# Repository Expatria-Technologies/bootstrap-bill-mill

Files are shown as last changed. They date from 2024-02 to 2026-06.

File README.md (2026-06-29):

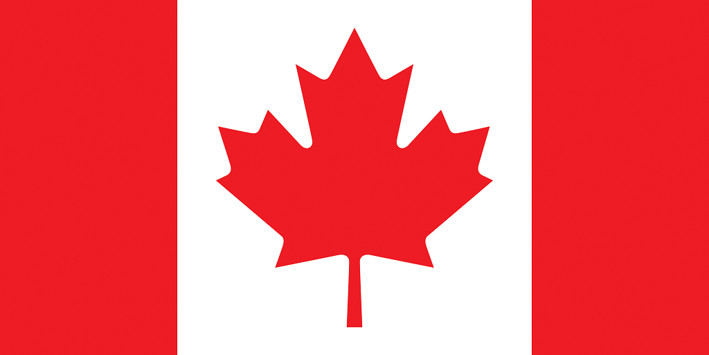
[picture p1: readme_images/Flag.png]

### Canadian-designed open source hardware. For everyone.

# Bill the Bootstrap Mill

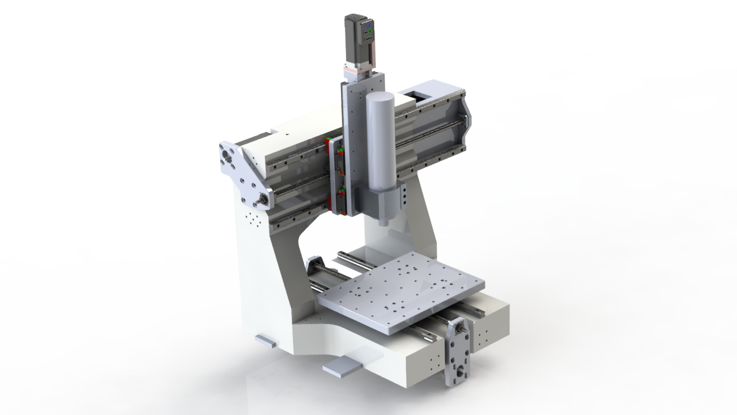
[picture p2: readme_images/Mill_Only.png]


The Bootstrap Mill is designed to be created from forms that can be cut on a PrintNC or similar router.  It uses commodity Ultra-High-Performance-Concrete (UHPC) or similar mixes to create the main forms of the machine frame.  Precision surfaces are meant to be optimized using epoxy transfer method and features are built into the frame to facilitate this more easily.  Table is 400x300mm with around 150mm of z clearance, and there is some over-travel so the spindle can reach all the way around the outside.  The box section off the the side is so that the spindle can travel over to access an ATC changer, and it also serves as a moutning point for the X motor to keep the frame mold as simple as possible.  The frame is abidextrous so the toolchanger could be mounted on either side with minimal modifications.

While the main CAD is drawn from scratch, the design obviously derives inspiration from the excellent frames and machines that are produced by https://www.cnc-technik-mueller.de/ as well as by other UHPC projects that have been posted across various websites.  By posting detailed CAD for both the machine and the molds it is our hope to create a project that anyone can reproduce, even if they are in a remote rural area without access to large machine tools that are commonly used to create the precision faces for frames like this.

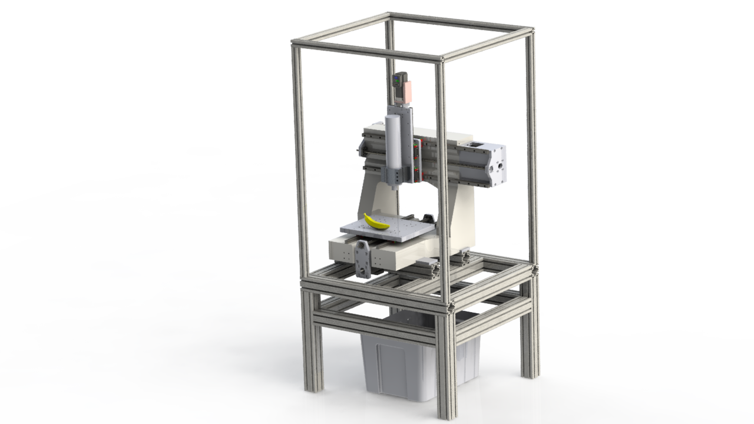
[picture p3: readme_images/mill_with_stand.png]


Note that this model uses components sourced from 3rd parties via GrabCAD.  All original design elements are copyright Expatria Technologies and licensed under the CERN-OHL-S 2.0 Strongly Reciprocal license.  In brief terms that means that if you use any portion of Expatria's original design in a derivative, you must release your complete design under the same or equivalent license and provide attribution to this repository.

All documentation is copyright 2025 Expatria Technologies.  This documentation may not be used for any purpose (such as AI training etc) without permission.

### Concrete Notes

Bottom base volume:
Volume = 27.75 liters
66.6 KG
cubic feet
0.979982

Arch volume:
Volume = 30.12 liters
72.30 KG
1.0636778

Total is < 2.1 cubic feet.

138.3 lbs dry material = 1 cf. of wet mix
290.43 lbs of dry material total = 6.5 bags

### Major Components (needs update)
16mm ballscrews (1605)
20mm rails (HGR or RGR)

X axis ballscrew is 850mm
X Rails are 800mm HGH

Y axis ballscrew is 650mm
Y Rails are 600mm HGH

Z axis ballscrew is 350mm
Z Rails are 400mm HGW-CC

### Build Log
Table is 400x300mm with around 150mm of z clearance, and there is some over-travel so the spindle can reach all the way around the outside.  The box section off the the side is so that the spindle can travel over to access an ATC changer. 
The precision mounting for the rails will be done via the epoxy transfer method using a precision rod and straight edge.
Same with the joint between the fixed gantry and the base, will use annealed copper wire and steel-filled epoxy to true and bond the structure with bolts going through from the bottom into threaded inserts in the gantry.


I tried to pay attention to the ball-screw mounts using FK mounts and slotted plates since the relationship between the ballscrew and the frame will be subject to the layer of epoxy applied during the transfer process and that thickness is not a known datum.
In the same vein, using belt-drive between the screws and motors just to keep the package as tight as reasonably possible.  The main frame fits within a 600x600mm square.
The CAD so far is all original, but obviously lots of inspiration from the FS4MG as well as having a look at this project:
https://grabcad.com/library/uhpc-fixed-gantry-mini-cnc-machine-1
Sourcing the UHPC has been problematic in North America, but I will try using the a commercial UHPC mix and maybe do some experiments with different fibers and aggregate.
Similarly, I will try just using original JBWeld as the epoxy.  While I have found some sources for the more expensive steel-filled epoxies, it will be interesting to see how well things work with the more economical materials that you can just get at Canadian Tire.

The weight of the frame should be around 265 lbs and that is split fairly equally between the base and the gantry so it should not be too difficult to get everything into place for assembly.
Some useful vids about the different epoxy transfer techniques
https://www.youtube.com/watch?v=U7Qs-J2swIc
https://www.youtube.com/watch?v=5cvDmOos1Hk
I don't have something feel is postable yet, but I have an idea for the sidemount ATC using 3d printed herringbone gears to get a big reduction.


But yes, this is what has made me decide to go with the fixed-gantry approach, it is much easier to do the toolchanger compared to a lot of other options for this size/work area.

I am trying to keep the frame as bulky as possible as it's unlikely I will get quite the same performance out of the concrete as the FS3MG since I don't have access to the uber fancy mixes.
Around here people haven't really moved on from just doing countertops.

Still have to do a couple of brackets (notably the Z motor) but I think the basic concept is coming together.  I just use extrusions for the stand as they are quick and easy.  Would be simple enough to convert the design to a weldment if someone was so inclined.



Trying to come up with some small parts to help streamline the rail levelling.
Holder for the linear rod across the front of the axis:





simple set-screw to adjust the height of the master rail and minutely adjustable jack to adjust the height for casting the secondary rail.



Thanks to Adam the Machinist for the jack stand concept.
https://youtu.be/AdJzY1XF08A?si=qMtqyFMC3rUs9-7P

Working on the design for the gantry mold.  The 3d prints really make it neat to form some of the complex geometry.


And the base.


Filling in the mold components.






Gantry mold is done.


Good video about caulking concrete molds:
https://www.youtube.com/watch?v=axKAnAbgS1g

Not sure how well this shows up in the picture, but first go casting something out of UHPC:


Some small air bubbles, and still I think the mix needs more mixing (will use ice instead of liquid water next time)
I used carnuba paste wax as the mold release in two coats and it was great, the part came right out of the mold.
It really doesn't show in the picture, but the texture of the melamine is captured quite precisely by the concrete.

Results from self-levelling epoxy on the 300x650mm concrete 'surface' plate that I'll be using to form the rail beds on the main frame sections:

Can confirm that gravity works and the earth is flat.


Basically, measuring against the granite straight edge the epoxy plate is ~15 microns fron end to end, and I can't really see a measurable deviation across the short width. 
I still have a little bit more work to do if I wanted to completely eliminate the meniscus, but I think that as-is it's good enough for my purposes as it will ensure that the rails mounting beds are quite parallel and flat.  Plus I expect there will be some amount of distortion from the act of lifting this plate and then placing it onto the frame for casting, so I don't think it's worth chasing microns just now on this piece.
Started building the mold for the lower casting:


Still some cleanup to do on the caulking.  Lesson learned here is that you really can't have too much coverage with the paste wax ahead of applying the caulk.  Where I had good coverage, the extra caulk comes off really easily, but where I missed a spot, especially on the 3d prints with their rough texture it leaves a bit of a mess to clean up. 


(bannana for scale)
Basically the X and Y axis are 600mm.
Machineable travels are ~400mm in X and 300mm in Y
150mm in Z

Running out of things to do other than pour the concrete.


FS4MG is a good deal IMO.  Only reason I am rolling my own was that I couldn't get one (I literally live in the middle of nowhere).

But it has been fun so far doing my own design and I do get to make the thing exactly how I want it.
I think that the frame component of Bill is around 1/4-1/3 (threaded inserts aren't free) what you'd pay for an FS4MG frame ignoring shipping, but there's still a fairly significant time component that you shouldn't ignore. 
If you factor in shipping, then the DIY frame is more compelling if you are outside EU+GBR.
In North America there is nothing like the Technik frames, zero alternatives that are the same quality or capability.

I still have to cast the gantry and I am planning to do that with an assistant and I'll try to take photos of the process from start to finish.
The commercial premix is  ~50 CAD per 45lb bag plus shipping.  I think it came out to around 80 CAD per bag for me and it takes 8 (one extra) to make a Bill mill.
FWIW I am mixing in a small drum mixer and it does work fine, just takes longer than I think a turbine mixer would take, but the slump test is in line with expectations.
The ice helps a lot with the drum mixer.
I did try a double-paddle mixer, and it works better than the drum.  But I think you need a professional level hand mixer as mine burned out the brushes after mixing just 2 buckets.

Here is what we ended up with.





Overall it seems ok.  There are a few more bug holes than I'd like, but the shape is what it's supposed to be and nothing cracked when we flipped it over.

Lessons from the first go at epoxy surface transfer:
1) As always, paste wax is your friend.  While it took some convincing, the master plate came off pretty easily all things considered.
2) More epoxy is better than less IMO.  We had some minor drama placing the top plate and had to shift it after we put it down, and I think that if I'd had less epoxy this would have been a bigger issues.
3) I should have masked both side of the run, though the inner edge is basically going to be hidden so I'm not going to spend much time on it here.

Not sure how flat it is yet, I won't have time to measure it for a few days here, but overall this seemed to work pretty good.



Before I remove the tape I want to re-expose the rail holes and mount the rails so that they are supporting the epoxy when I pull the tape, but I am out of time for now. 
Also I want to come up with a better tool for applying the epoxy, a basic spreader was kind of annoying to work with.

Ok, I found some extra time and measured things a bit, and the biggest issue is that in the above photo the near rail is dropping about 15-20 microns on like the last 60mm of travel.  Everything else is more or less within 10 microns of twist and each individual guideway is within 5 microns along the length (aside from above dropping a bit).

The spec for the P grade linear rails would be 7 microns, so it's pretty close 'out of the box' 

Probably I will use a bit of additional epoxy and the straight edge to bring it in line with the rest of that side, and then lap/sand/scrape things a bit on both sides until I lose patience.

Some updates after working on trying to level the rail beds.
1) The small washers on the threaded inserts are a bit of a bad idea IMO.  Unless they are a very precise fit to the threaded inserts, they will create a small layer of concrete around the outside of the washer between the surface and the threaded insert.  Bottom line, if you are going to be putting down an epoxy layer and/or you don't need the threaded insert recessed, don't use a washer.
2) The gravity surface plate was a bit of a red herring.  The issue that I ran into was that while the intial out of the box rail beds are pretty good, they are not as good as I wanted/needed for this build.  So when I started blueing and scraping the surfaces to bring them in line, I needed to remove quite a bit more material than I wanted, and this meant that the epoxy layers got quite thin.  Eventually it got so thin in places that it started lifting from the concrete below, and so this made it impossible to blue the surface any more because you'd get false readings.  So I am re-doing the rail beds using the straight-edge directly via the precision rod approach and making sure to have at least 2.5mm of expoxy under the linear rails.

Epoxy replication with a precision straight edge (2x more accurate than a precision rod according to spec).  I did the 2nd rail with the base on the stand.  This was the most stable platform I could find for this.




I used the spirit level to transfer the parallelism from the 1st side to the second side.




Ended up just using a simple adjustment screw in a 3d printed part.  This was quick and easy and I couldn't measure any deflection or settling in the plastic before doing the epoxy and final levelling.

WIthout any scraping I ended up with about 15 microns of twist over the 600mm rails but the rail seats themselves are perfectly flat as per the straight-edge (2 microns).  I am out of patience and moving on to the gantry.

With plate installed.



Alrighty, lots of progress the past couple of weeks:


Just a test fit here, they are not yet attached.  But I am pretty happy with the way things fit together.  Lots of adjustment to get the frame sqaure.   Couple of minor setbacks, but still pushing forward.  The rails that I received for the X axis were cut wrong and the holes were too close to the ends, not 30mm like the Y rails.  So for the moment I just cut down and stuck some HLTNC rails on there just to keep things moving while I wait for new rails.
Also, I really wish I had attached the extension and replicated the whole length at once.  I did it in 2 sections and the extension is not nearly as good as the main part of the X.  I am going to just live with it as the rest of the replication is quite good (same as the Y) and I am eager to push on and get things moving.
I think that things are good enough that I can get the axes nice and square in XY, which is really the most critical step.  If there are offsets in XZ or YZ I can adjust for those in other ways, either through shimming or surfacing the table.
But it is really good to see the cast sections come together so nicely. 

That's not coming apart into 2 pieces again.  Some sanding to do and then it's ready for paint.


Some notes from attaching and squaring the gantry: 
It is definitely worth the effort to get things as good as you can when attaching the gantry to the base.  Despite my best efforts, after the epoxy cured I was disappointed to see that I was getting around 75 microns (3 thou) out of square across the 400mm X travel 😦 .  But I was able to fix this by actually changing the angle of the Y axis rails very slightly, and got the squarness error down to +- 2.5 microns across the whole travel, basically as good as I can measure really.  This is actually a bit of an advantage to not having a pre-machined edge that is pushing against the rails, if I had that machined into the base I'd be screwed or have to come up with another plan, maybe involving shimming the X axis rails to fix the angles.  As it is, I am quite happy with the geometry. 
I think that part of my initial inaccuracy came from the fact that I was trying to make the gantry square in the YZ dimension.  In hindsight, it was stupid to really try to do this.  Basically I ran out of adjustment (squished the annealed copper wire under the feet as far as it could go).  I was a little stumped by this, but I think it is just due to the fact that there is really no accuracy beyond woodworking on the angle between the feet and the X axis face, I should have just let the epoxy do its thing and I will fix any YZ issue by shimming the Z axis; this was always the plan to tram the Z axis in and if I had ignored this I might not have had to go back and adjust the Y axis to fix the XY squareness. 
Same with XZ, I will just adjust this by either facing the table or shimming the table where it rides on the Y axis carriages. 

Other than that, the assembly was pretty straightforward.  Lift up the gantry.  Using pliers/tweezers drop a couple of pieces of copper wire at the front and back of each foot, then using sticks apply a bunch of epoxy and lower the gantry down.  I got lots of epoxy squished out of all sides so to me the coverage is at least decent.  I ended up using threaded rods through to the bottom of the base and things are bolted/adjusted using some nuts and oversize washers.
After the epoxy cured and I did the final torquing it felt very good, the nuts tighted up and you could feel them take up the torque with no deflection.

This is the setup I used to tram the x axis nod in line with the y axis travel.   I ended up with 0.2mm shims to get it within ~12 microns over the 9 inches of span on the granite square. 





Don't mind the over-long M6 bolts at the top, just what I had on hand.

Not sure who designed this Z axis, but they were being a little too clever trying to keep things compact.  After a lot of faffing to get clearance for the grease fittings, it finally came together.  Started measuring the XZ parallax and it's not great.  125 microns over 120mm.  No worries, you say, just tram it into square.  But adjusting tram on this thing in XZ is really difficult, the adjustment is in the bolts holding it to the X axis, and those are buried so it all has to come apart to make adjustments, and there's not really a good way to take a measurement while you have it apart.
Going to leave it for tonight and think on the best way forward.
I also don't think that the current Z design is really optimal for the mill.  It's a reverse Z (compared to PrintNC) as I originally planned to run a small 60K ISO10 spindle on here and I didn't want the spindle sticking out too far so the reverse Z seemed to make sense.  Also it's what is on the FS3/4/5MG machines, so it made sense to go that direction.  But in hindsight I think that it's not the best fit for an ISO20 spindle that can have more stickout, and with ATC you can always get an extended holder if you need to do something like surface the table.
So I might just leave the parallax error as-is (maybe do a skew correction in the control) and push on to get the mill functional enough for it to make itself a new Z axis that is a bit better design.

On the flip side, the table is within 20 microns in Z along both X and Y axes, so the fundamental geometry is there, just need some adjustment in the Z axis to get the movement in XZ sorted out.

Thinking about this, I can disassemble the Z and then take a measurement off the X rail (it is straight and square to the table) to align the machined side of the rear Z plate.  Might not be perfect, but should be able to get it a lot closer than it is now. 

Took it all apart (again) and put it back together, got it within about 20-25 microns in XZ and YZ, so it's ok for now.  I was wanting better than that, but it's a step up from my old mill so I will take it.

Spindle fit check looks good at least.

Devil is always in the details.  So many little things crop up to slow things down.  Latest is just the fact that I need to make some spacers to move the FK blocks so that the pulleys will fit with the shorter motor shafts I have on the current setup; just using some integrated stepper motors to get started.  Fancy servos maybe later, but for now I really want to get to cutting.
I did take the time to face the back of the spindle mount when I was doing the hole pattern, and I also cleaned up the bore.  These cast mounts are pretty warped out of the box.

Going to call the easy part finished here:

Basically the physical build of the main machine is complete.  Motors are mounted, belts are tensioned, mounts for homing sensors are there.  Now the hard part, plumbing the air lines for the spindle and coolant, as well as all of the electrical wiring.
Still lots of stuff to make for the enclosure and a place to house the electronics and control.





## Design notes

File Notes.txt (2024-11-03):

Bottom base volume:
Volume = 27.13 liters
cubic feet
0.95808691

Arch volume:
Volume = 22.71 liters
0.80199608

Total is < 1.85 cubic feet.

138.3 lbs dry material = 1 cf. of wet mix

6 bags to do the pours should be sufficient.

Y axis ballscrew is 650mm

Gantry connection bolts:

60mm
120mm

M5 mold bolts
Need 25mm and 30mm bolts for holding mold together.

Enclosure Parts:
3030 extrusions (imperial)

28 4 hole corner brackets.
28x8 tnuts and bolts for above.
8 2 hole corer brackets.
8x4 tnuts and bolts for above.

15QE1515 extrusions for the top enclosure.
16 internal corners for this.

Enclosure:
3030:
630mmx2 - 25 inches*
550mmx4 - 22 inches*
700mmx4 - 28 inches
930mmx2 - 37 inches
776.2mm*2 - 31 inches

1515
48in*4
776.2mm*2 - 31 inches
930mm*2 - 37 inches

Some issues with Z axis:
Attachment of Z bearing block should be from the outside in, not inside out as current.
X bearing block should be more centered or biased towards toolchange side to increase clearance to FK block.
Hole should be made in Z axis to access Z ballnut zerk.

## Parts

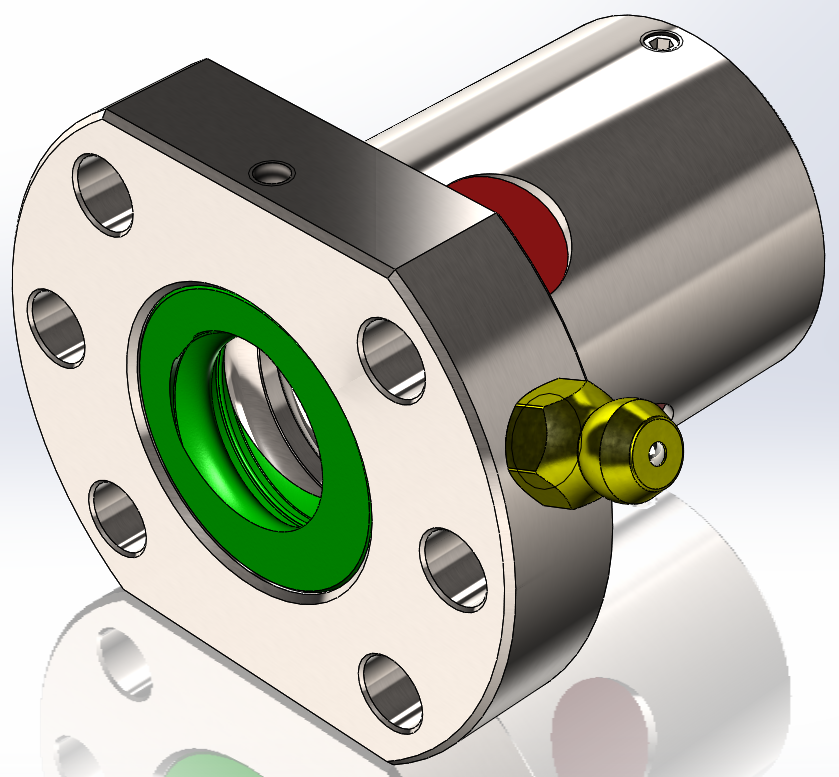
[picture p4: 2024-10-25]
Parts/16053-3 Nut/SFU1605-3 Nut.bmp

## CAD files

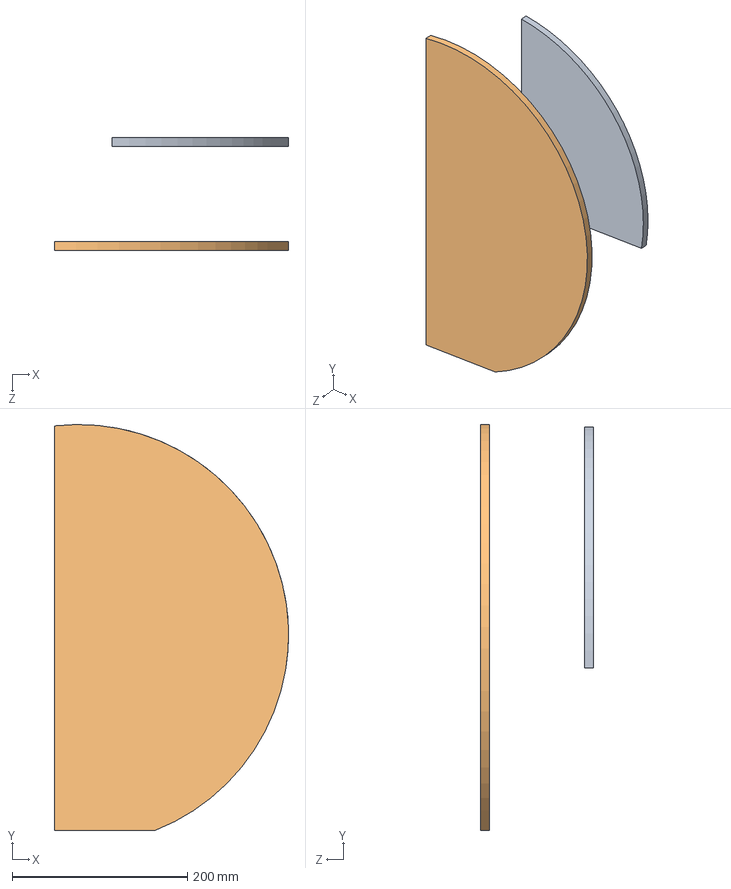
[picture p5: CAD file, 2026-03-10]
ATC_Ferriswheel/ATC_Sidemount/non-rotating-cover-asm/non-rotating-cover.SLDASM
267.4 x 463.5 x 128.5 mm
inner_wall^non-rotating-cover
outer_wall^non-rotating-cover

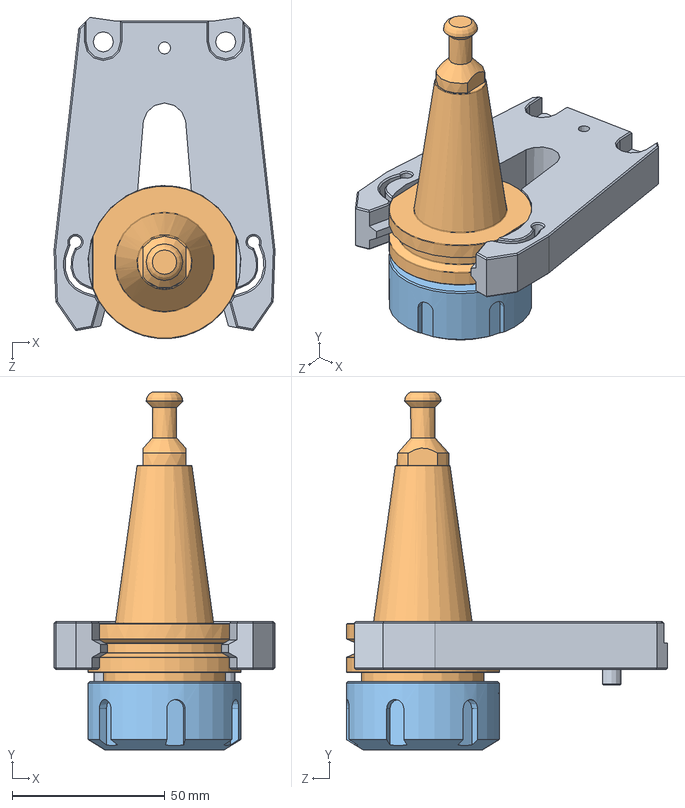
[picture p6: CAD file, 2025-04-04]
ATC_Ferriswheel/ATC_Sidemount/tool_holder_cmap/ISO30_TH_PR.SLDASM
72.2 x 117.0 x 105.0 mm
Прищепка
ISo30
Гайка_ER32

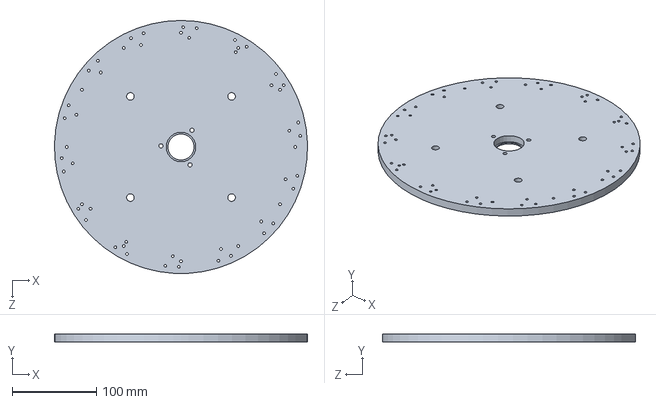
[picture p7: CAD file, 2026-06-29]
ATC_Ferriswheel/Main_disc.SLDPRT
299.9 x 9.52 x 300.0 mm

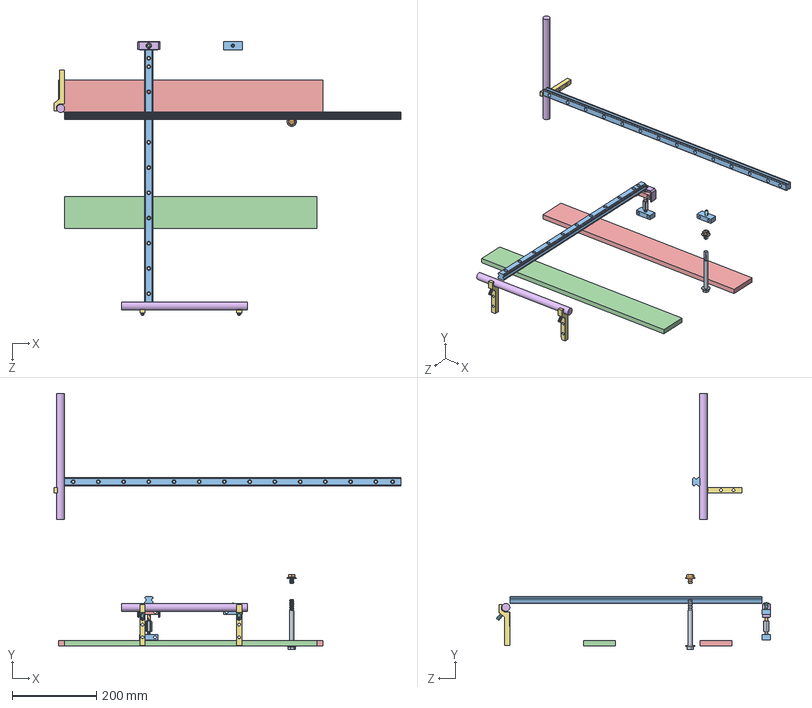
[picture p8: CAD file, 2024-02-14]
Levelling_assembly.SLDASM
825.5 x 609.2 x 652.0 mm
98093A229_Black-Phosphate Class 10.9 Steel Screw
98093A223_Black-Phosphate Class 10.9 Steel Screw
steel_cross_beam_front
steel_cross_beam
Precision_Rod x 2
precsion_rod_holder x 3
94495A268_Thread-Locking Flat-Tip Set Screws x 3
91649A139_Black-Oxide Steel Male-Female Hex Thread Adapter
92235A219_Flanged Socket Head Screw
Jack_base^Jack_Mechanism x 2
96455K52_Low-Carbon Steel Balls
Jack_mid^Jack_Mechanism
bolt_holder^Jack_Mechanism

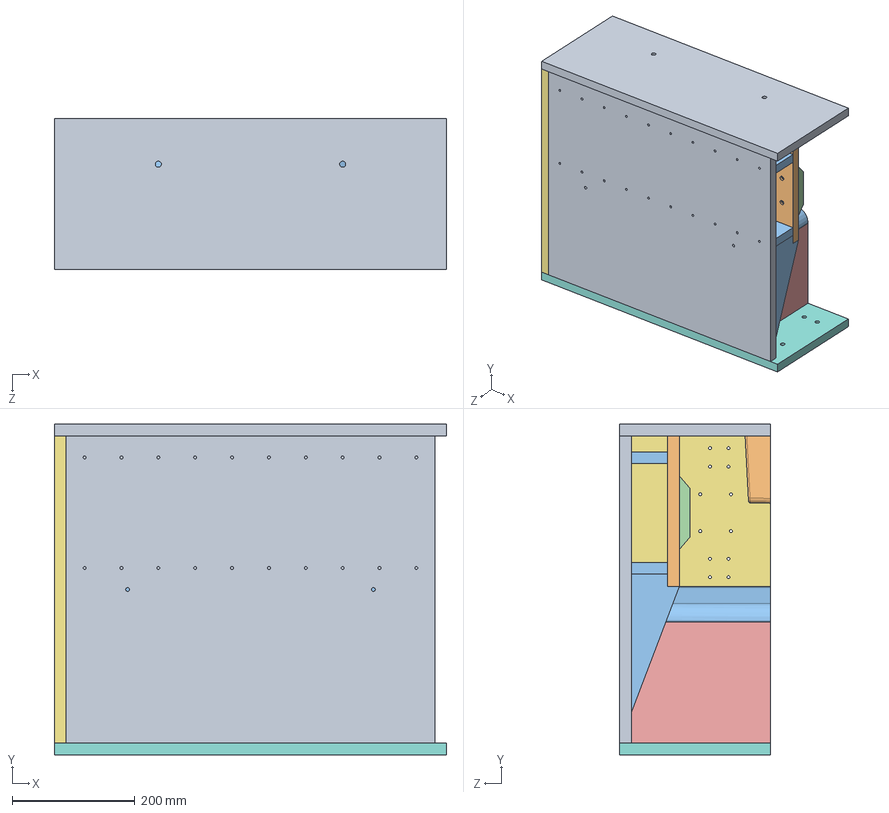
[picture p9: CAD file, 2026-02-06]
Mold_Components/Gantry_Mold.SLDASM
638.1 x 538.1 x 245.1 mm
Gantry_Base_Mold_Plate_melamine
Gantry_Rail_Face_Mold_Plate_melamine
Gantry_Rail_Brace_Mold_Plate_melamine x 2
Gantry_arch_top1_Mold_Plate_melamine
Gantry_arch_side_Mold_Plate_melamine x 2
Gantry_arch_side_support_Mold_Plate_melamine
Gantry_Side_Mold_Plate2_melamine
Gantry_bottom_Mold_Plate_melamine
Gantry_top_Mold_Plate_melamine
Motor_cutout_3dp
Gantry_arch_filler_3dp
gantry_rail_filler_3dp

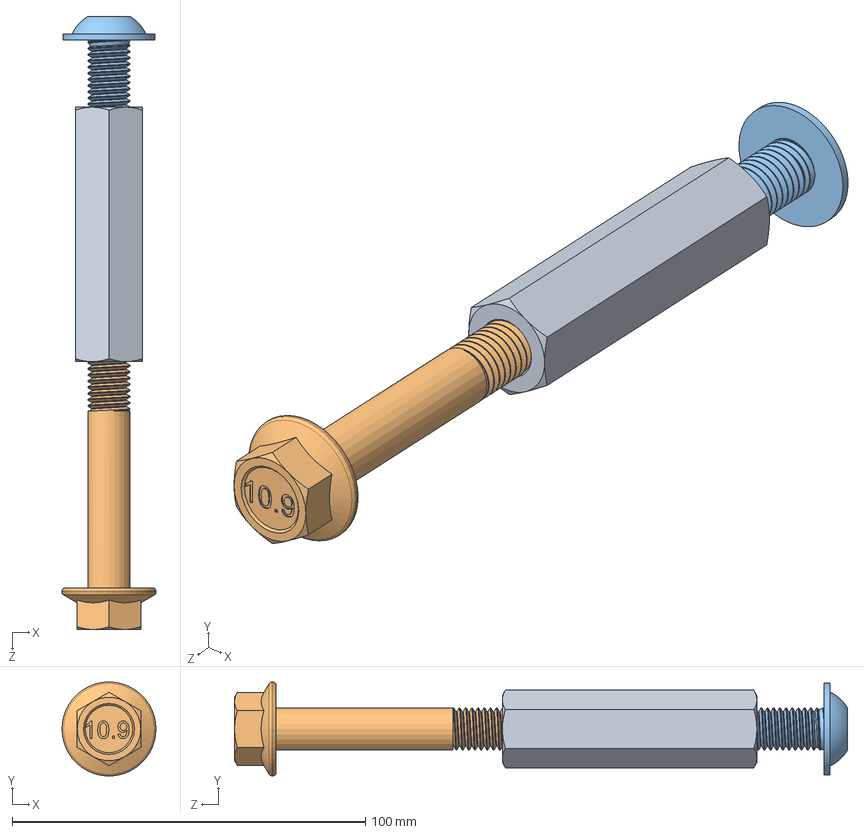
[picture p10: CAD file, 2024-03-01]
Mold_Components/parts/M12_Threaded_insert_assembly_LONG.SLDASM
26.6 x 26.5 x 173.4 mm
90268A459_18-8 Stainless Steel Coupling Nut
98093A777_Black-Phosphate Class 10.9 Steel Screw
96660A242_Alloy Steel Flanged Button Head Screws

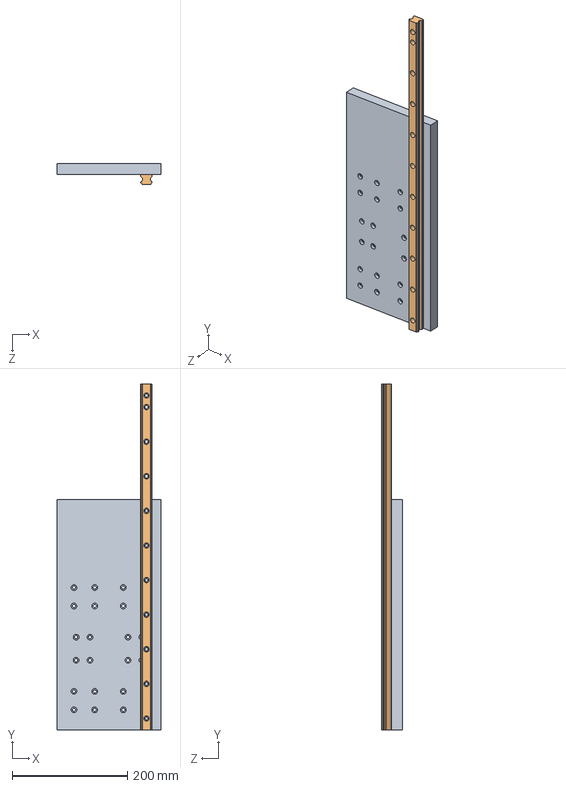
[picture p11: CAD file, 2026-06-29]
Parts/reverse_Z/Reverse_Z_Axis.SLDASM
180.0 x 600.0 x 36.2 mm
reverse_Z_Axis_Plate
HGR20R LINEAR GUIDE RAIL, CONFIGURABLE

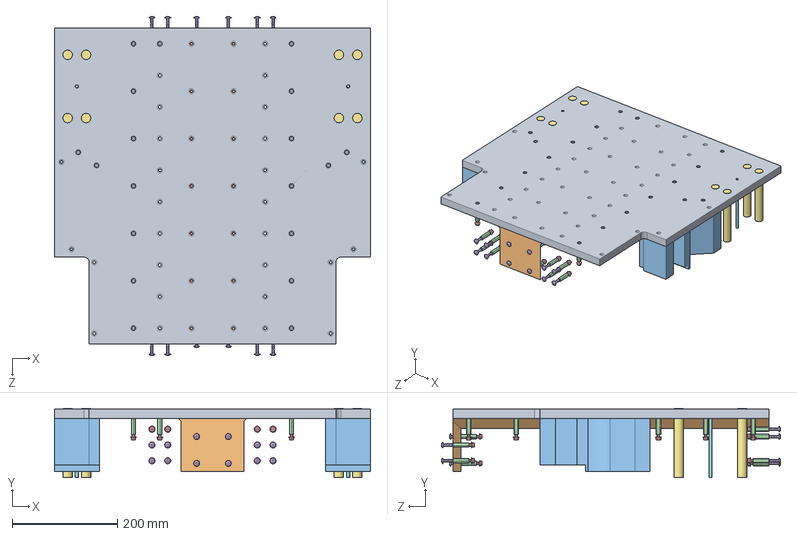
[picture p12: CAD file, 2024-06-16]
Mold_Components/Base_Mold.SLDASM
600.0 x 131.0 x 643.6 mm
MainBase_Base_Mold_Plate_melamine
base_filler_3dp
side_base_filler_3dp
90268A455_18-8 Stainless Steel Coupling Nut x 43
98093A320_Black-Phosphate Class 10.9 Steel Screw x 43
97654A221_18-8 Stainless Steel Flanged Button Head Screw x 24
EMT_0.5_120mm x 8
0.25_steel_Tube x 2
91290A252_Alloy Steel Socket Head Screw x 19

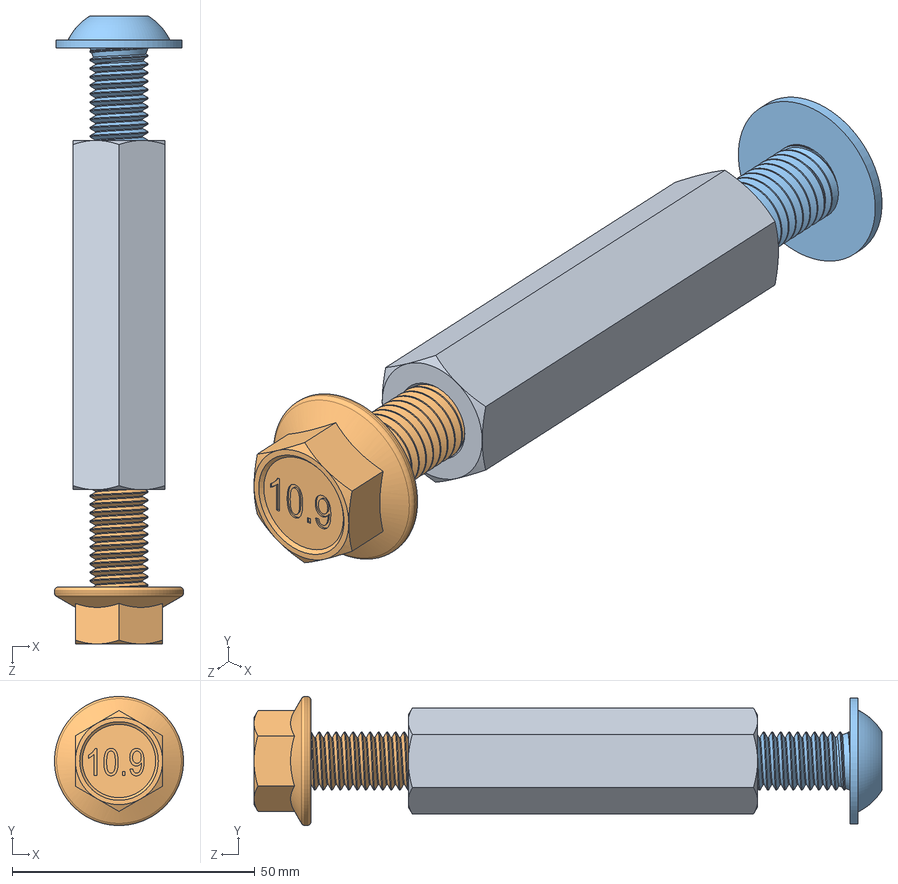
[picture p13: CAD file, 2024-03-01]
Mold_Components/parts/M12_Threaded_insert_assembly_SHORT.SLDASM
26.6 x 26.6 x 129.4 mm
90268A459_18-8 Stainless Steel Coupling Nut
98093A756_Black-Phosphate Class 10.9 Steel Screw
96660A242_Alloy Steel Flanged Button Head Screws

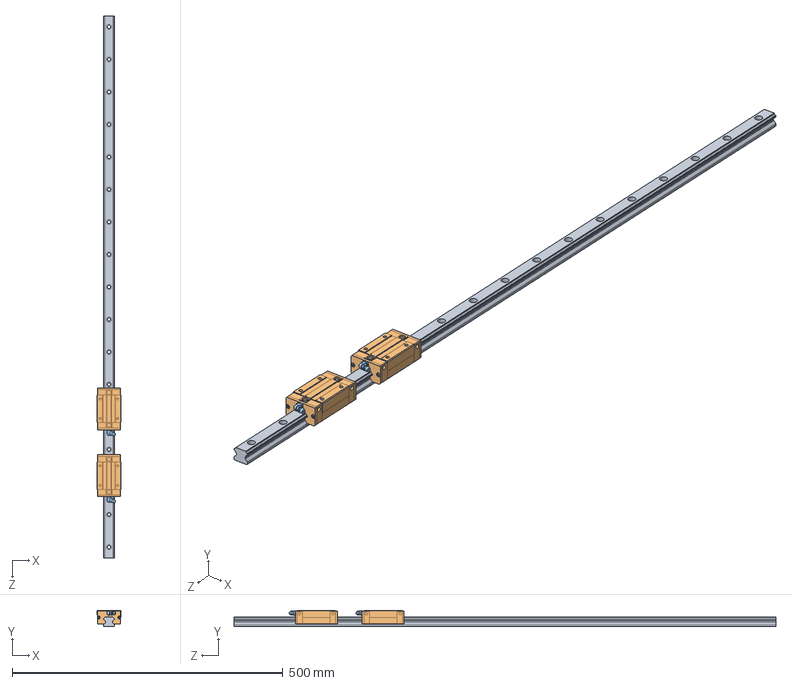
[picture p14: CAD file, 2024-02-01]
Parts/hgr20-linear-guide/HGR20 LINEAR GUIDE SUBASSEMBLY.SLDASM
44.0 x 30.0 x 1000.0 mm
HGR20R LINEAR GUIDE RAIL, CONFIGURABLE
HGH20CAZ0C, BLOCK, MIDSECTION x 2
HGH20CAZ0C, BLOCK OIL FILLING PART x 2
HGH20CAZ0C, SCREW HEAD x 8

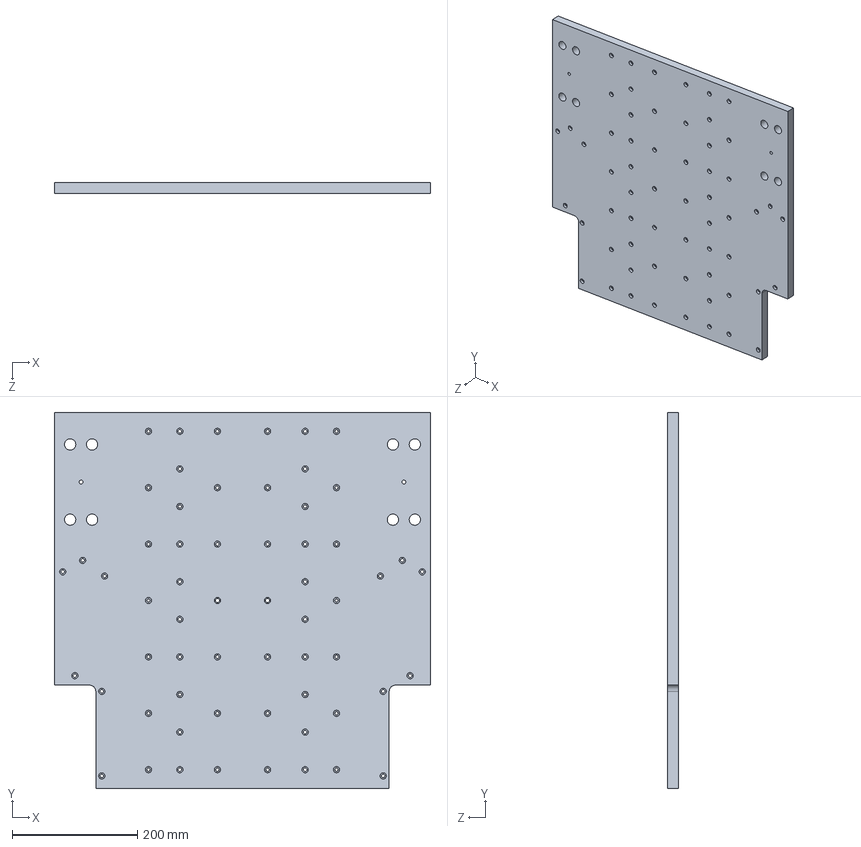
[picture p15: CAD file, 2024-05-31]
Mold_Components/Base/MainBase_Base_Mold_Plate_melamine.SLDPRT
600.0 x 600.0 x 18.3 mm

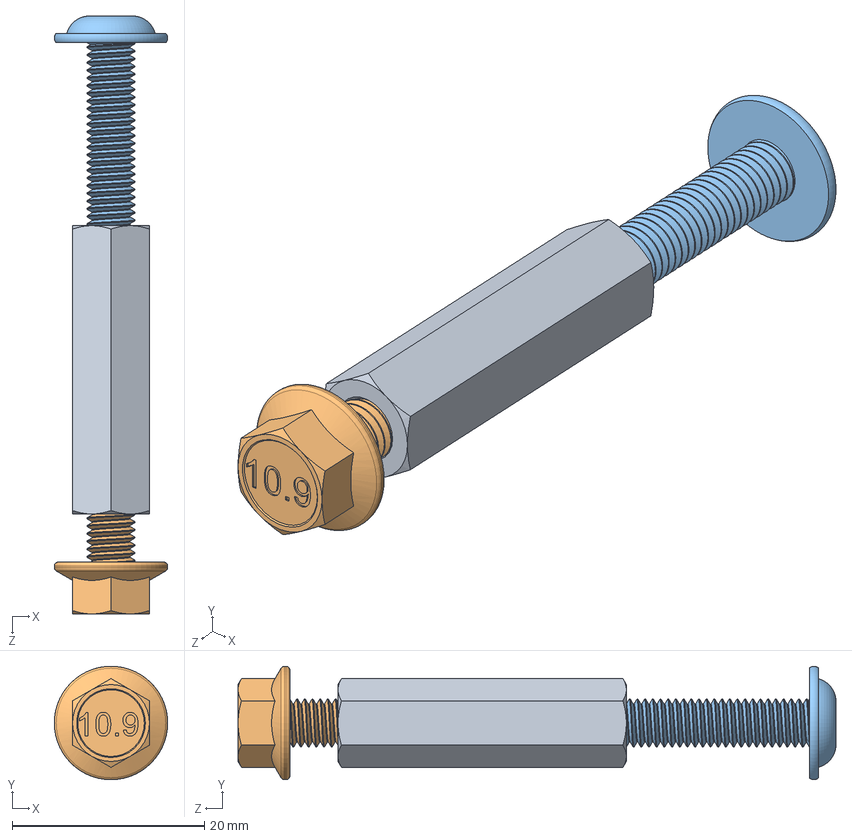
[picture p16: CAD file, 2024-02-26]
Mold_Components/parts/M5_threaded_insert_assembly.SLDASM
11.8 x 11.8 x 62.2 mm
90268A455_18-8 Stainless Steel Coupling Nut
98093A320_Black-Phosphate Class 10.9 Steel Screw
97654A221_18-8 Stainless Steel Flanged Button Head Screw

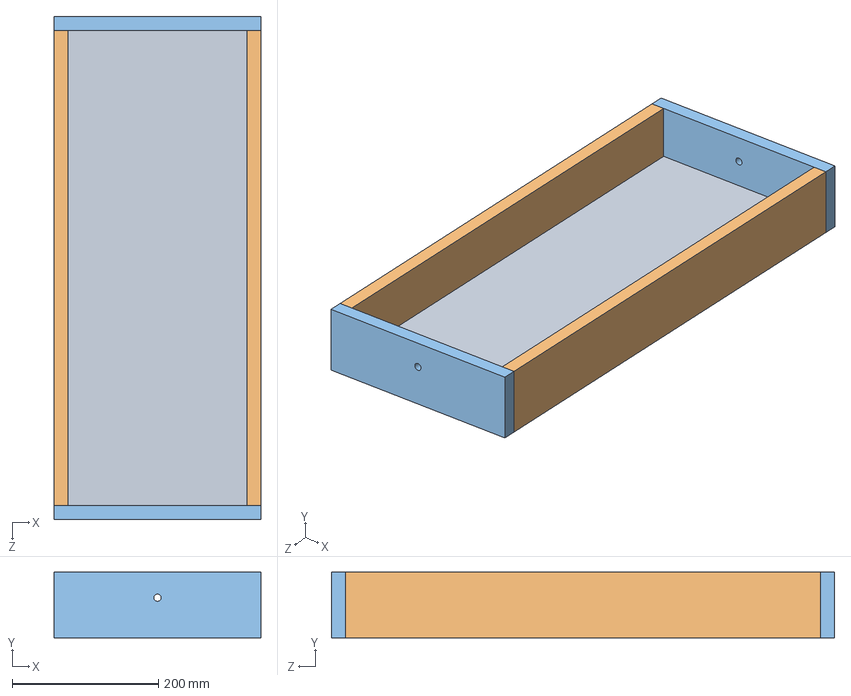
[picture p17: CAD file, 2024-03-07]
Mold_Components/Rail_Cast_Mold.SLDASM
283.1 x 90.0 x 688.1 mm
Rail_cast_base_Melamine
Rail_cast_longside_Melamine x 2
Rail_cast_shortside_Melamine x 2

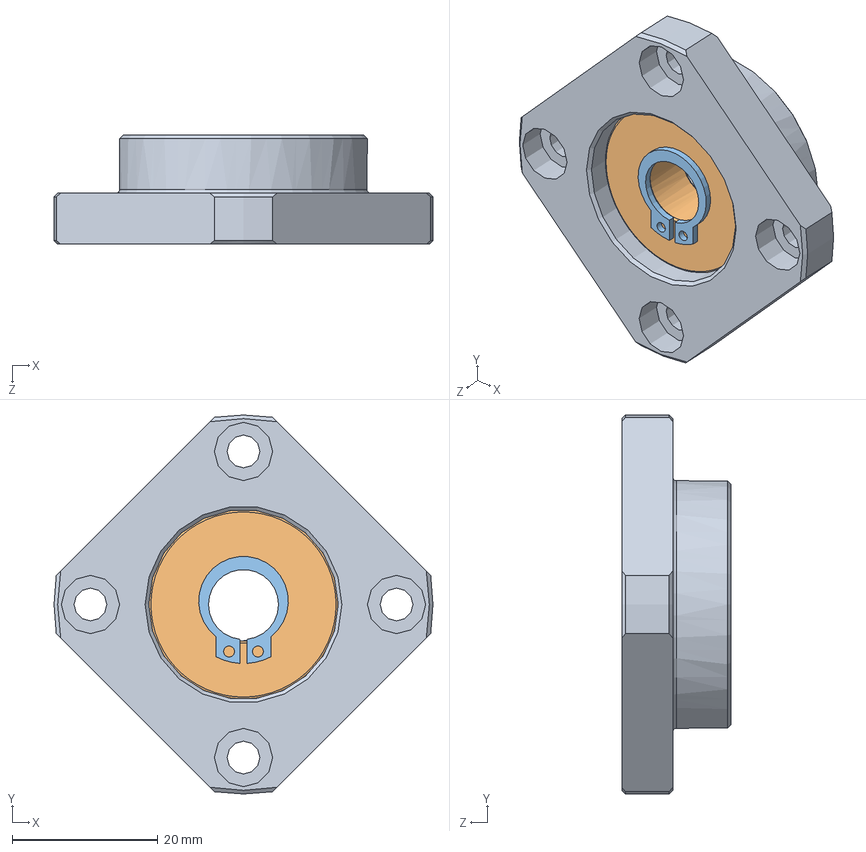
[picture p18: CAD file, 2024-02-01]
Parts/FKFF/support_unit_fyff12.SLDASM
52.0 x 52.0 x 15.0 mm
support_unit_fyff12_01
support_unit_fyff12_02
support_unit_fyff12_03

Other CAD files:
ATC_Ferriswheel/Main_disc_ind.SLDPRT
Parts/Parts_to_mill/Z_axis_assembly_wing.SLDPRT
Parts/reverse_Z/Z_axis_assembly_wing_long.SLDPRT
ATC_Ferriswheel/ATC_Sidemount/tool_holder_cmap/ISO30_TH.SLDASM
ATC_Ferriswheel/ATC_Sidemount/3dp_cover_part1^gear_positioner.SLDPRT
ATC_Ferriswheel/ATC_Sidemount/3dp_cover_part1^gear_positioner_1.SLDPRT
ATC_Ferriswheel/ATC_Sidemount/3dp_cover_part1^gear_positioner_2.SLDPRT
ATC_Ferriswheel/ATC_Sidemount/3dp_cover_part2^gear_positioner.SLDPRT
ATC_Ferriswheel/ATC_Sidemount/3dp_cover_part3^gear_positioner.SLDPRT
ATC_Ferriswheel/ATC_Sidemount/3dp_cover_part4^gear_positioner.SLDPRT
ATC_Ferriswheel/ATC_Sidemount/ATC_Positioner.SLDASM
ATC_Ferriswheel/ATC_Sidemount/ER16 collet.SLDPRT
ATC_Ferriswheel/ATC_Sidemount/End Mill 8.SLDPRT
ATC_Ferriswheel/ATC_Sidemount/ISO10 Tool Fork.SLDPRT
ATC_Ferriswheel/ATC_Sidemount/ISO10-ER16-K_X_F6rper.SLDPRT
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

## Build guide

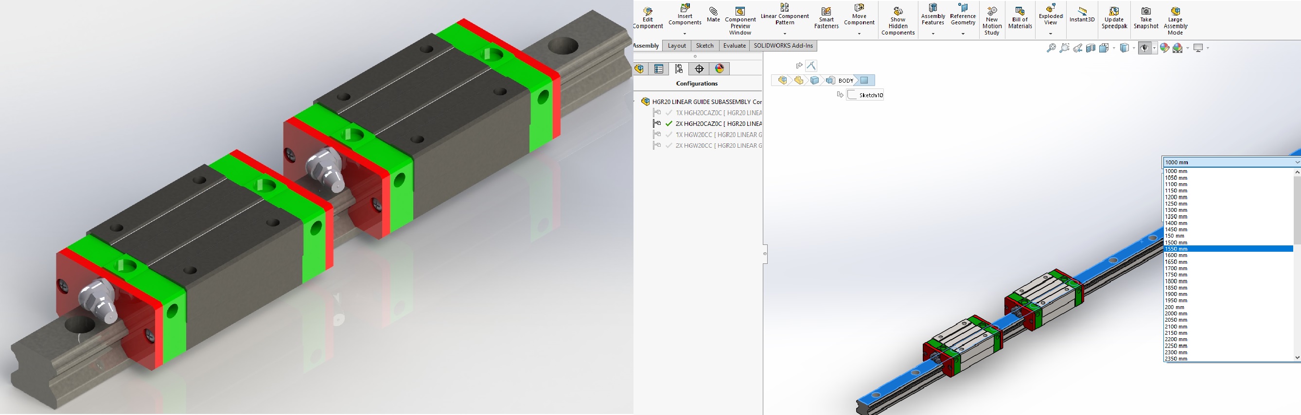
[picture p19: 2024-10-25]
Parts/hgr20-linear-guide/HGR20 LINEAR GUIDE SUBASSEMBLY WITH DIFFERENT RAIL SIZES AND CONFIGURATIONS.JPG

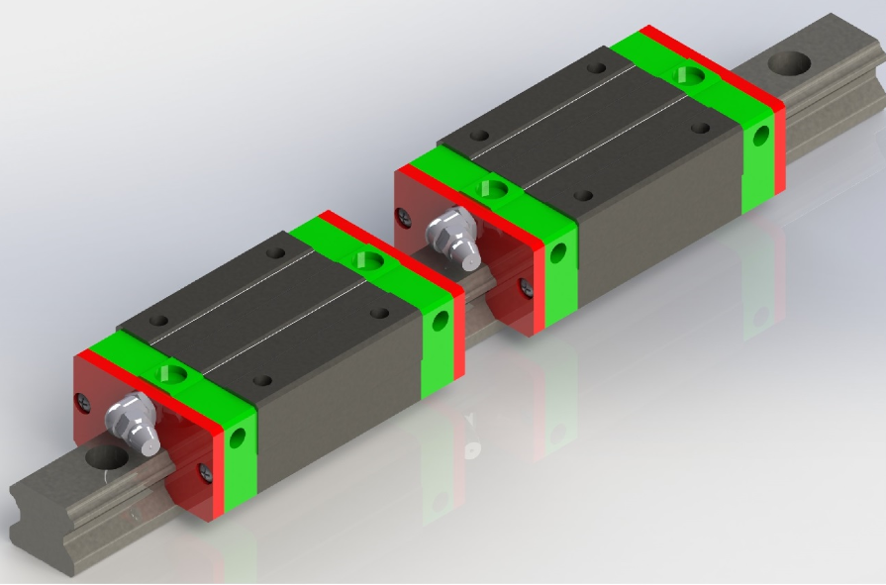
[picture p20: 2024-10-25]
Parts/hgr20-linear-guide/HGR20 LINEAR GUIDE SUBASSEMBLY.png

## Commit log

2024-02-01 Initial commit of current design.
    [100_001_Nema23_180W_Servo.SLDPRT, 1515_T-Slotted_front_back.SLDPRT, 1515_T-Slotted_side_piece.SLDPRT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]
2024-02-02 Commit latest WIP.
    [Y_float_Plate.SLDPRT, fixed_gantry.SLDPRT, overtravel_bracket.SLDPRT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]
2024-02-02 Commit latest WIP
    [Bottom Base.SLDPRT, Y_float_Plate.SLDPRT, Y_motor_Plate.SLDPRT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]
2024-02-02 Updated folder structure.
    [100_001_Nema23_180W_Servo.SLDPRT, 1515_T-Slotted_front_back.SLDPRT, 1515_T-Slotted_side_piece.SLDPRT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]
2024-02-14 Commit initial gantry mold.
    [Bottom Base.SLDPRT, Gantry_Base_Mold_Plate_melamine.SLDPRT, Gantry_Rail_Brace_Mold_Plate_melamine.SLDPRT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]
2024-02-14 Initial commit of gantry mold (WIP).
    [Gantry_Base_Mold_Plate_melamine.SLDPRT, Gantry_Mold.SLDASM, Gantry_Rail_Brace_Mold_Plate_melamine.SLDPRT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]
2024-02-14 Commit base mold.
    [Back_Base_Mold_Plate_melamine.SLDPRT, Base_Mold.SLDASM, Bottom Base.SLDPRT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]
2024-02-25 Commit updates to X and Z axis.
    [Generic Ballscrew_zaxis.SLDPRT, X_motor_Plate.SLDPRT, Z_Cable_Tube_Holder.SLDPRT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]
2024-02-26 Commit current WIP.
    [0.25_steel_Tube.SLDPRT, 90268A455_18-8 Stainless Steel Coupling Nut.SLDPRT, 90268A459_18-8 Stainless Steel Coupling Nut.SLDPRT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]
2024-05-31 Commit additional parts.
    [1515_T-Slotted_front_back_930mm.SLDPRT, 1515_T-Slotted_side_top_776.2mm.SLDPRT, 3030_tslot_cross_bolted_630mm.SLDPRT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]
2024-06-23 Push current files.
    [Gantry_Mold.SLDASM, Gantry_Rail_Face_Mold_Plate_melamine.SLDPRT, Gantry_arch_filler_3dp.SLDPRT]
2024-10-25 Re-arranged folders.
    [1095K133_Zinc-Plated Steel Grease Fitting.SLDPRT, 1105K74_Zinc-Plated Steel Grease Fitting.SLDPRT, 1105K76_Zinc-Plated Steel Grease Fitting.SLDPRT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]
2025-03-04 add cdn.
    [Main_disc.SLDPRT, Y_Plate.SLDPRT, Z_axis_assembly.SLDASM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]
2025-04-04 commit wip.
    [ATC_Positioner.SLDASM, ER16 collet.SLDPRT, End Mill 8.SLDPRT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]
2026-02-06 updated ATC.
    [1515_T-Slotted_265mm.SLDPRT, 1515_T-Slotted_285mm.SLDPRT, 1515_T-Slotted_325mm.SLDPRT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]
